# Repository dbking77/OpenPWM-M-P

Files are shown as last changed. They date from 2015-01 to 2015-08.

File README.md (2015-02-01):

OpenPWM-M-P
===========

A single channel motor driver for dc brushed motors utiliizing a attiny and a ZXBM5210 motor driver

At this time, this project is distributed under the TAPR Open Hardware License: http://www.tapr.org/ohl.html

These drivers use a resistor to control the max trip current. 

We assume that the desired trip current is right at the max for the driver, ow, 2 amps. 

Using the examples supplied in the data sheet, we would need a 0.25 ohm Rs resistor. Though, that resistor would need to be a 1 watt resistor. 

We would like to make the resistor smaller than a 1 watt surface mount resistor. So, we made the pad a 0805 pad. The max dissipation you can get out of a 0805 resistor is 1/3 watt. 

By altering VRef, we can alter the power disapated by the resistor. 

The resistor will see connect upto VRfef and ground.

If we select a lower cost resistor of 0.047 ohms ( http://www.digikey.com/scripts/DkSearch/dksus.dll?Detail&itemSeq=165686396 )

The equation for what the trip current(assuming that the trip current is 2) is:

ItripMax(2) = Vref / (Rs * 10)
2 = Vref / 0.47
Vref = 0.94V

The resistor should only see 0.04 watts if Vref is kept to 0.94.

Project owned by Michael Gregg(mgregg@-at-@michaelgregg.com) and Derr(dbking77@-at@gmail.com)

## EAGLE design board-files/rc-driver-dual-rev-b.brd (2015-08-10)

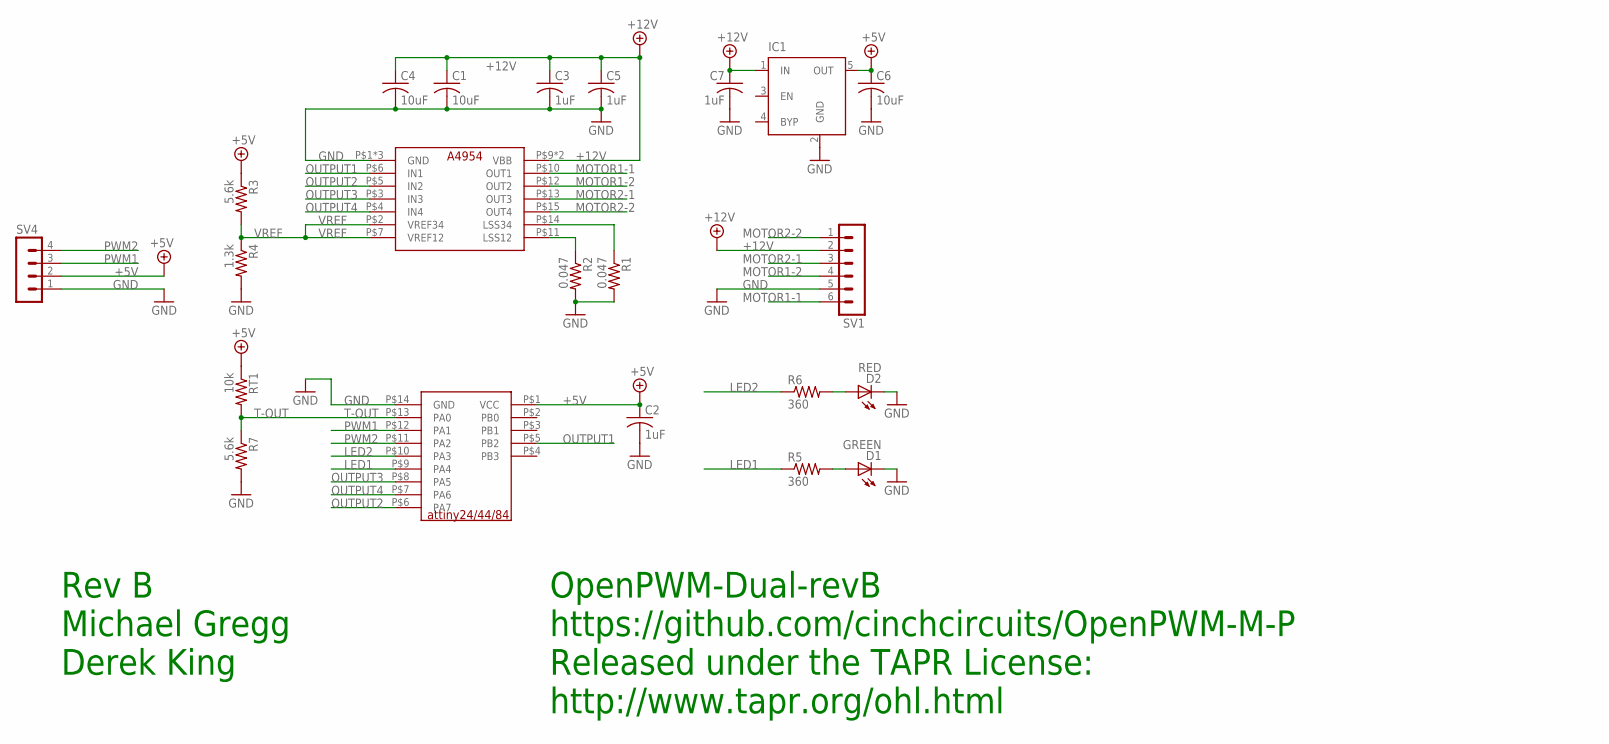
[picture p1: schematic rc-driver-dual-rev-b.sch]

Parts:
C1, C4, C6: 10uF; C1206
C2, C3, C5, C7: 1uF; C0603
D1: GREEN; CHIPLED_0603
D2: RED; CHIPLED_0603
IC1: MIC5219XX; SOT23-5; MPN TPS70950
R1, R2: 0.047; R0805
R3, R7: 5.6k; R0603
R4: 1.3k; R0603
R5, R6: 360; R0603
RT1: 10k; R0603
SV1: MA06-1
SV4: MA04-1
U$1: ATTINY24A; SOIC-14-WIDE
U$2: A4954-DUAL-HBRIDGE; TSSOP-16-LP

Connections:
+5V: C2.1, C6.1, IC1.5 (OUT), R3.1, RT1.1, SV4.2, U$1.P$1 (VCC)
+12V: C1.1, C3.1, C4.1, C5.1, C7.1, IC1.1 (IN), SV1.2, U$2.P$9 (VBB), U$2.P$16 (VBB)
GND: C1.2, C2.2, C3.2, C4.2, C5.2, C6.2, C7.2, D1.C, D2.C, IC1.2 (GND), R1.2, R2.2, R4.2, R7.2, SV1.5, SV4.1, U$1.P$14 (GND), U$2.P$1 (GND), U$2.P$8 (GND), U$2.P$17 (GND)
LED1: R5.1, U$1.P$9 (PA4)
LED2: R6.1, U$1.P$10 (PA3)
MOTOR1-1: SV1.6, U$2.P$10 (OUT1)
MOTOR1-2: SV1.4, U$2.P$12 (OUT2)
MOTOR2-1: SV1.3, U$2.P$13 (OUT3)
MOTOR2-2: SV1.1, U$2.P$15 (OUT4)
unnamed: R1.1, U$2.P$14 (LSS34)
unnamed: R2.1, U$2.P$11 (LSS12)
unnamed: D2.A, R6.2
unnamed: D1.A, R5.2
OUTPUT1: U$1.P$5 (PB2), U$2.P$6 (IN1)
OUTPUT2: U$1.P$6 (PA7), U$2.P$5 (IN2)
OUTPUT3: U$1.P$8 (PA5), U$2.P$3 (IN3)
OUTPUT4: U$1.P$7 (PA6), U$2.P$4 (IN4)
PWM1: SV4.3, U$1.P$12 (PA1)
PWM2: SV4.4, U$1.P$11 (PA2)
T-OUT: R7.1, RT1.2, U$1.P$13 (PA0)
VREF: R3.2, R4.1, U$2.P$2 (VREF34), U$2.P$7 (VREF12)

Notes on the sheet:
OpenPWM-Dual-revB
https://github.com/cinchcircuits/OpenPWM-M-P
Released under the TAPR License:
http://www.tapr.org/ohl.html
Rev B
Michael Gregg
Derek King

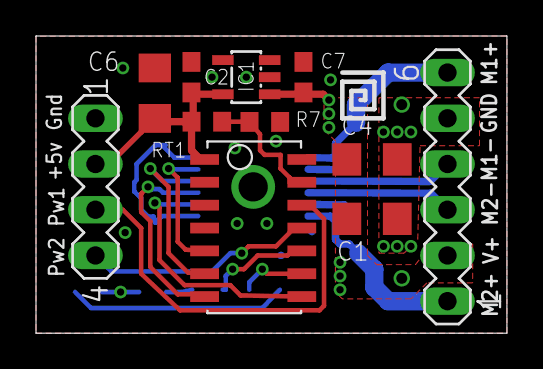
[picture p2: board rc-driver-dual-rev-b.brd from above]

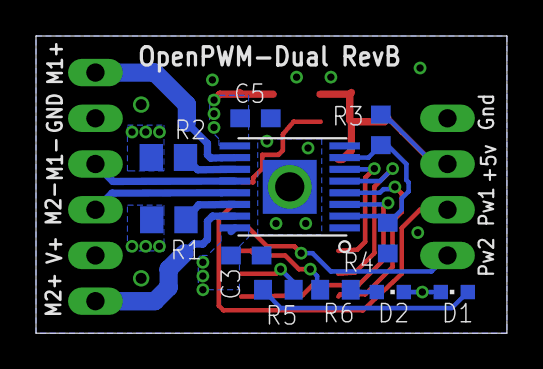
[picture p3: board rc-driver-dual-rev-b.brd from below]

Board: 2 copper layers, 26.2 x 16.5 mm, 22 parts (11 on the bottom side), 21 nets.

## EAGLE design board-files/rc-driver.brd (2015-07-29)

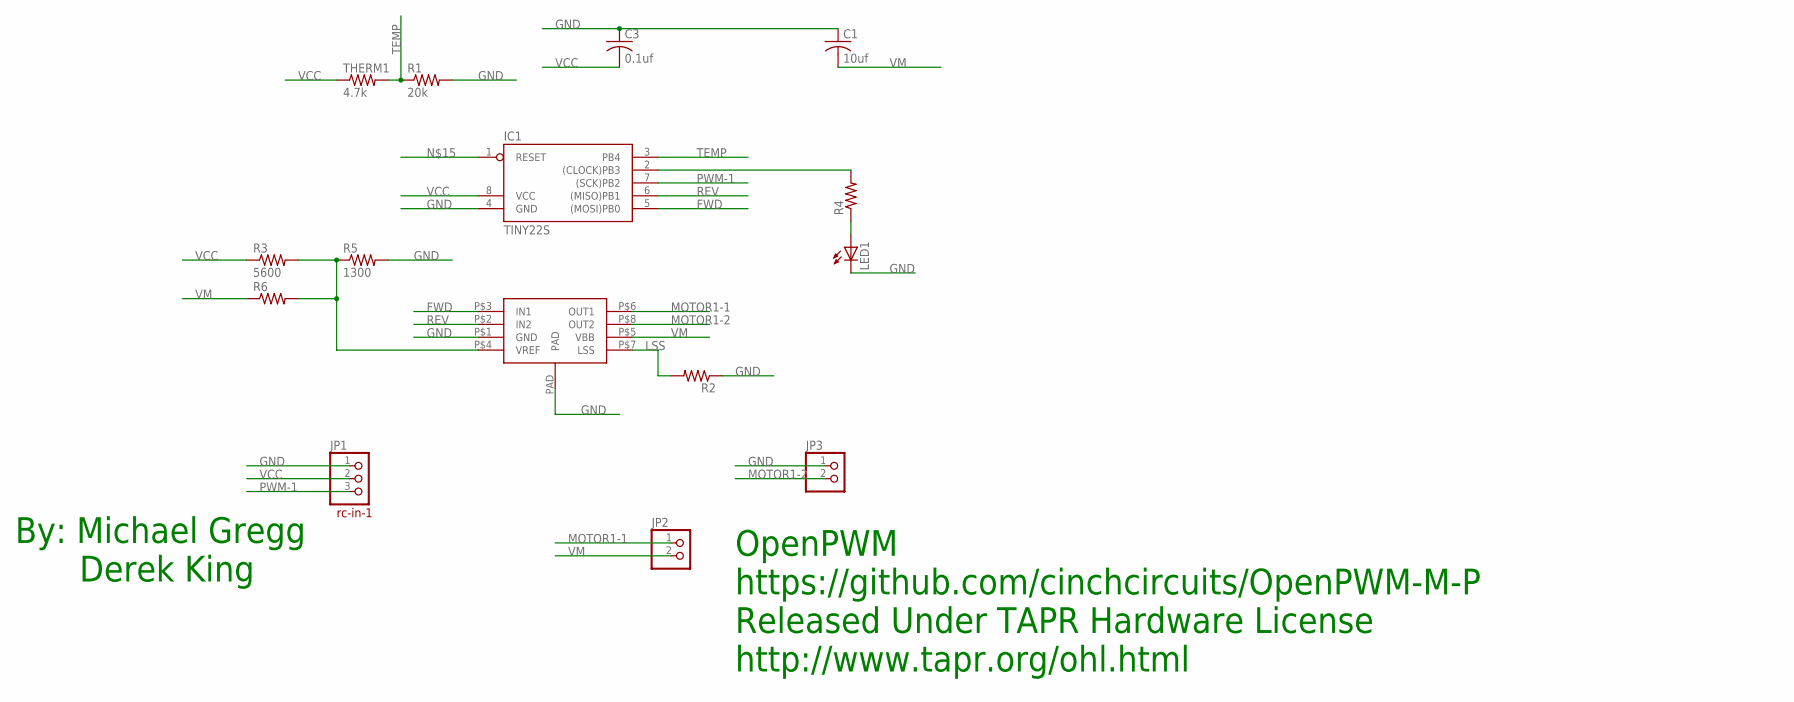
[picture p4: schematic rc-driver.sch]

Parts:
C1: 10uf; C1210
C3: 0.1uf; C0805
IC1: TINY22S; SOIC8
JP1: PINHD-1X3; 1X03
JP2, JP3: PINHD-1X2; 1X02
LED1: LEDCHIP-LED0603; CHIP-LED0603
R1: 20k; R0603
R2: R-US_R0805W; R0805W
R3: 5600; R0603
R4, R6: R-US_R0603; R0603
R5: 1300; R0603
THERM1: 4.7k; R0603
U$1: A4950-HBRIDGE; SO-8EP

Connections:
FWD: IC1.5 ((MOSI)PB0), U$1.P$3 (IN1)
GND: C1.1, C3.1, IC1.4 (GND), JP1.1, JP3.1, LED1.C, R1.2, R2.1, R5.2, U$1.P$1 (GND), U$1.PAD
LSS: R2.2, U$1.P$7 (LSS)
MOTOR1-1: JP2.1, U$1.P$6 (OUT1)
MOTOR1-2: JP3.2, U$1.P$8 (OUT2)
unnamed: R3.2, R5.1, R6.2, U$1.P$4 (VREF)
unnamed: IC1.2 ((CLOCK)PB3), R4.2
unnamed: LED1.A, R4.1
PWM-1: IC1.7 ((SCK)PB2), JP1.3
REV: IC1.6 ((MISO)PB1), U$1.P$2 (IN2)
TEMP: IC1.3 (PB4), R1.1, THERM1.2
VCC: C3.2, IC1.8 (VCC), JP1.2, R3.1, THERM1.1
VM: C1.2, JP2.2, R6.1, U$1.P$5 (VBB)

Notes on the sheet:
rc-in-1
By: Michael Gregg
Derek King
OpenPWM
https://github.com/cinchcircuits/OpenPWM-M-P
Released Under TAPR Hardware License
http://www.tapr.org/ohl.html

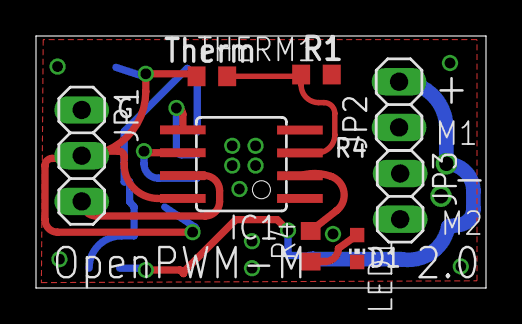
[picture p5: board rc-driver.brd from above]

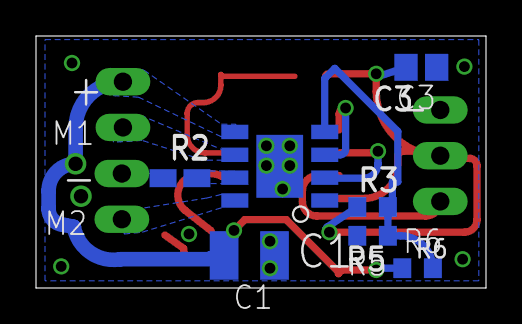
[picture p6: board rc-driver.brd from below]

Board: 2 copper layers, 25.0 x 14.0 mm, 15 parts (7 on the bottom side), 13 nets.

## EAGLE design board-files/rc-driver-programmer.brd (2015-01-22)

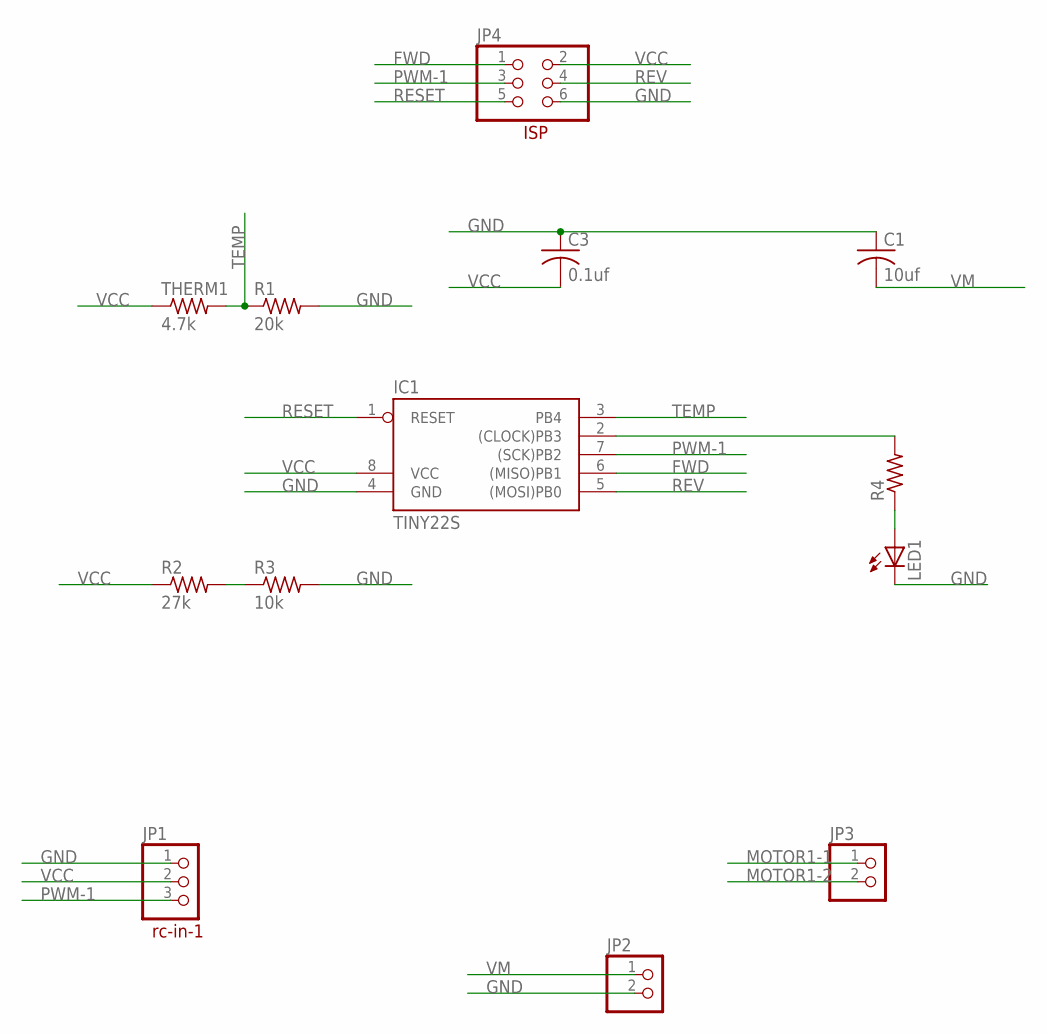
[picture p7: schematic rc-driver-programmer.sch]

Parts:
C1: 10uf; C1210
C3: 0.1uf; C0805
IC1: TINY22S; SOIC8
JP1: PINHD-1X3; 1X03
JP2, JP3: PINHD-1X2; 1X02
JP4: PINHD-2X3; 2X03
LED1: LEDCHIP-LED0603; CHIP-LED0603
R1: 20k; R0603
R2: 27k; R0603
R3: 10k; R0603
R4: R-US_R0603; R0603
THERM1: 4.7k; R0603

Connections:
FWD: IC1.6 ((MISO)PB1), JP4.1
GND: C1.1, C3.1, IC1.4 (GND), JP1.1, JP2.2, JP4.6, LED1.C, R1.2, R3.2
MOTOR1-1: JP3.1
MOTOR1-2: JP3.2
unnamed: IC1.2 ((CLOCK)PB3), R4.2
unnamed: LED1.A, R4.1
unnamed: R2.2, R3.1
PWM-1: IC1.7 ((SCK)PB2), JP1.3, JP4.3
RESET: IC1.1 (RESET), JP4.5
REV: IC1.5 ((MOSI)PB0), JP4.4
TEMP: IC1.3 (PB4), R1.1, THERM1.2
VCC: C3.2, IC1.8 (VCC), JP1.2, JP4.2, R2.1, THERM1.1
VM: C1.2, JP2.1

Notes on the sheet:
rc-in-1
ISP

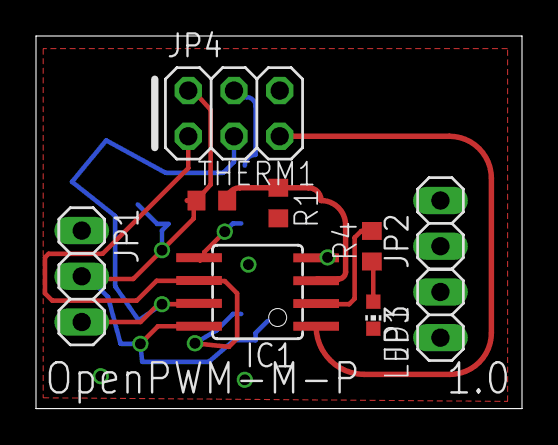
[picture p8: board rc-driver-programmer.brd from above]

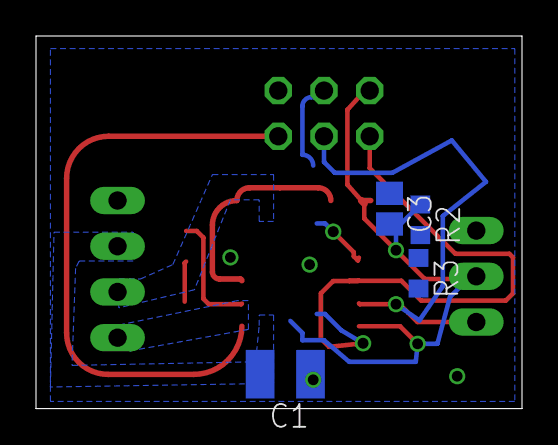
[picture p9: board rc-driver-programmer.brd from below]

Board: 2 copper layers, 27.0 x 20.7 mm, 13 parts (4 on the bottom side), 11 nets.

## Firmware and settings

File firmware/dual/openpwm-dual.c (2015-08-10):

/*
 * Copyright (c) 2015, Derek King
 * All rights reserved.
 *
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
 * THIS SOFTWARE IS PROVIDED BY THE COPYRIGHT HOLDERS AND CONTRIBUTORS "AS IS"
 * AND ANY EXPRESS OR IMPLIED WARRANTIES, INCLUDING, BUT NOT LIMITED TO, THE IMPLIED
 * WARRANTIES OF MERCHANTABILITY AND FITNESS FOR A PARTICULAR PURPOSE ARE DISCLAIMED.
 * IN NO EVENT SHALL THE COPYRIGHT HOLDER OR CONTRIBUTORS BE LIABLE FOR ANY DIRECT,
 * INDIRECT, INCIDENTAL, SPECIAL, EXEMPLARY, OR CONSEQUENTIAL DAMAGES (INCLUDING, BUT
 * NOT LIMITED TO, PROCUREMENT OF SUBSTITUTE GOODS OR SERVICES; LOSS OF USE, DATA,
 * OR PROFITS; OR BUSINESS INTERRUPTION) HOWEVER CAUSED AND ON ANY THEORY OF LIABILITY,
 * WHETHER IN CONTRACT, STRICT LIABILITY, OR TORT (INCLUDING NEGLIGENCE OR OTHERWISE)
 * ARISING IN ANY WAY OUT OF THE USE OF THIS SOFTWARE, EVEN IF ADVISED OF THE
 * POSSIBILITY OF SUCH DAMAGE.
 */

#include <stdint.h>

#define F_CPU 8000000UL
#include <util/delay.h>
#include <avr/interrupt.h>
#include <avr/io.h>

/* 
 * Getting compiler and tools (in Ubuntu)
 *  sudo apt-get update
 *  sudo apt-get install binutils-avr gcc-avr avrdude avr-libc
 */


/*
 * Fuses : want to run at 8Mhz off of internal oscillator
 * 
 * Extended Fuse Byte : 0xFF
 * unused [7:1]   
 * SELFPRGEN 0    : 1   : Self-prgromming enabled   : no
 *
 * High Fuse Byte : 11011111b = 0xDD
 * RSTDISBLE 7    : 1   : External reset disabled   : no
 * DWEN      6    : 1   : DebugWIRE active          : no
 * SPIEN     5    : 0   : Serial Program Enabled    : yes
 * WDTON     4    : 1   : Watchdog timer always on  : no
 * EESAVE    3    : 1   : EEPROM preserver on erase : no EEPROM not presevered
 * BODLEVEL [2:1] : 111 : Brownout Dectector level  : ?
 *
 * Low Fuse Byte : 11100010b = 0xE2
 * CKDIV8   7     : 1   : Clock Divided By 8        : don't divide by 8 (8Mhz internal osc)
 * CKOUT    6     : 1   : Clock output enabled      : no
 * SUT      [5:4] : 10  : Start-up time             : 14Clock cycles + 64ms
 * CLKSEL   [3:0] : 0010: Clock select              : calibrated internal osc
 *
 * http://www.engbedded.com/fusecalc/
 *  -U lfuse:w:0xe2:m -U hfuse:w:0xdf:m -U efuse:w:0xff:m
 */


/* 
 * Notes
 *   avr-gcc -print-file-name=include 
 *   g/usr/lib/gcc/avr/4.5.3/include
 *   /usr/lib/avr/include/avr/iotn24a.h
 */


// TODO have template class for this?
#define OUT1_PORT PORTB
#define OUT1_DDR DDRB
#define OUT1_PIN 2

#define OUT2_PORT PORTA
#define OUT2_DDR DDRA
#define OUT2_PIN 7

#define OUT3_PORT PORTA
#define OUT3_DDR DDRA
#define OUT3_PIN 5

#define OUT4_PORT PORTA
#define OUT4_DDR DDRA
#define OUT4_PIN 6

#define TOUT_PORT PORTA
#define TOUT_DDR DDRA
#define TOUT_PIN 0

#define PWM1_PORT PORTA
#define PWM1_DDR DDRA
#define PWM1_PIN 1

#define PWM2_PORT PORTA
#define PWM2_DDR DDRA
#define PWM2_PIN 2

// Used to indicate error has occurred
#define LED2_PORT PORTA
#define LED2_DDR DDRA
#define LED2_PIN 3

// Used to indicate that input signal is being recv'ed
#define LED1_PORT PORTA
#define LED1_DDR DDRA
#define LED1_PIN 4


void gpioInit()
{
  DDRA = 
    (0<<TOUT_PIN) |
    (0<<PWM1_PIN) |
    (0<<PWM2_PIN) |
    (1<<LED2_PIN) | 
    (1<<LED1_PIN) |
    (1<<OUT3_PIN) |
    (1<<OUT4_PIN) |
    (1<<OUT2_PIN) ;
  
  PORTA =
    (1<<PWM1_PIN) |
    (1<<PWM2_PIN) |
    (1<<LED2_PIN) |
    (1<<LED1_PIN) ;
  
  DDRB = 
    (1<<OUT1_PIN);
  
  PORTB = 0;
}

/*
 * Mapping of Timers to Outputs
 *  output1 and output2 are a pair
 *  output2 and output4 are a pair
 *  
 *  output1 : PB2 : OC0A
 *  output2 : PA7 : OC0B
 *  output3 : PA5 : OC1B
 *  output4 : PA6 : OC1A
 */


/**
 * Set duty for motor1 (out1 and out2)
 *    value of 255 = full forward
 *    value of -255 = full reverse
 *    value of 0 = stop/brake
 * 
 * out1 = PB2 = OC0A
 * out2 = PA7 = OC0B
 */
void setMotor1(int16_t duty)
{
  // Enable outputs, by enable PWM control of pins
  // set A & B outputs to non-inverting (for fast PWM)
  // in non-inverting mode pins are SET at BOTTOM
  enum { T0_COMv = 2 }; 
  TCCR0A |= (T0_COMv<<COM0A0) | (T0_COMv<<COM0B0);

  // Staturate duty between -0xFF and 0xFF
  if (duty > 0xFF)
  {
    duty = 0xFF;
  }
  else if (duty < -0xFF)
  {
    duty = -0xFF;
  }

  if (duty < 0)
  {
    OCR0A = duty-1;
    OCR0B = 0xFF; // 0xFF high always
  }
  else 
  {    
    OCR0A = 0xFF; // 0xFF high always
    OCR0B = -duty-1;
  }
}

/**
 * Set duty for motor2 (out3 and out4)
 *    value of 255 = full forward
 *    value of -255 = full reverse
 *    value of 0 = stop/brake
 * 
 * out3 = PA5 = OC1B
 * out4 = PA6 = OC1A
 */
void setMotor2(int16_t duty)
{
  // Enable outputs, by enable PWM control of pins
  // set A & B outputs to non-inverting (for fast PWM)
  // in non-inverting mode pins are set at BOTTOM, and cleared on compare match
  enum { T1_COMv = 2 }; 
  TCCR1A |= (T1_COMv<<COM1A0) | (T1_COMv<<COM1B0);

  // Staturate duty between -0xFF and 0xFF
  if (duty > 0xFF)
  {
    duty = 0xFF;
  }
  else if (duty < -0xFF)
  {
    duty = -0xFF;
  }

  if (duty < 0)
  {
    OCR1A = 0xFF&(duty-1);
    OCR1B = 0xFF; // 0xFF high always
  }
  else 
  {    
    OCR1A = 0xFF; // 0xFF high always
    OCR1B = 0xFF&(-duty-1);
  }
}


void disableMotors()
{
  // Disable outputs be switching pins to normal operation.
  // Out1 and out2 will PORT are already set to 0, so output will
  // high-Z and motor will coast
  TCCR0A &= 0x0F;  // Clears COM0A and COM0B (top 4 bits)
  TCCR1A &= 0x0F;
}



volatile uint8_t tim0_ovf_count = 0;
volatile char tim0_ovf_flag;
ISR(TIM0_OVF_vect)
{
  tim0_ovf_flag = 1;
  ++tim0_ovf_count;
}



// Prevent compiler from moving memory access operations across this code
#define MEMBAR() __asm volatile( "" ::: "memory" );

/** This struct allows use to create 16bit value from two 8bit values.
 *  It assumes that avrgcc organizes memory in little-endian order
 *
 * AVR uses 8bit registers, so 16bit value is stored two 8bit register
 * The typical code to concatinate two 8bit values into 16bit values is:
 *  
 *  uint8_t lo,hi;
 *  uint16_t result = (hi<<8) | lo;
 * 
 * The above code really shouldn't produce any assembly, because its just
 * shuffling around registers but it does:
 *    166:	83 2f       	mov	r24, r19
 *    168:	90 e0       	ldi	r25, 0x00	; 0
 *    16a:	92 2b       	or	r25, r18
 *    16c:	90 93 6d 00 	sts	0x006D, r25
 *    170:	80 93 6c 00 	sts	0x006C, r24
 *
 * If the union is used instead, the assembly looks like
 *    176:	c3 2f       	mov	r28, r19
 *    178:	d2 2f       	mov	r29, r18
 *    17a:	d0 93 6d 00 	sts	0x006D, r29
 *    17e:	c0 93 6c 00 	sts	0x006C, r2
 */
union Timer16
{
  uint16_t val;
  struct 
  {
    uint8_t lo,hi;
  };
};



/**
 * Returns 16bit timestamp generated from TCNT0
 */
uint16_t getTimestamp()
{
  union Timer16 cnt;
  cnt.lo = TCNT0;
  MEMBAR();
  cnt.hi = tim0_ovf_count;
  MEMBAR();
  uint8_t tifr = TIFR0;
  MEMBAR();

  // A servo PWM pulse is typically between 1.0 and 2.0 ms long.
  // Since clock is 8Mhz, this a 2.0ms pulse is 16000 cycles.
  // Unfortunately TIM0 is only 8bit (and TIM1 is set to only count to 8bit).
  // Just using the TCNT0 value to measure pulse width is not enough.
  // 
  // To generate top 8bits of 16bit time value, the timer overflow interrupt to
  // increment an 8bit overflow counter.  
  // Typically concatinating the overflow counter 8bit TCNT0 value produces 
  // will prodcue the correct overflow count.  
  // However, the is a race condition where the TNCT timer has overflowed
  // but the ISR has not run to increment the counter.
  // In this case the timer overflow flag will be set and TCNT will have a low
  // value.  In this case, the code should add 1 to the counter before using it.
  // There is is also the possibility that the timer overflows just after TCNT
  // is read, in this case the overflow flag will be set, and TCNT will be high,
  // in this case the overflow counter is correct.
  if ((tifr & (1<<TOV0)) && (cnt.lo & 0x80))
  {
    ++cnt.hi;
    // debug toggle LED everytime this occurs
    //LED2_PORT ^= (1<<LED2_PIN);
  }
  return cnt.val;
}


struct ServoPwm
{
  // pulse width measurement value of 8000 = 1ms.
  // value of zero is special and indicates valid value
  volatile uint16_t pulse_width;
  int16_t average_pulse_width;
  uint16_t rising_edge_time;
  volatile uint8_t no_signal_cycles;
  char valid_rising_edge; // true if rising edge was captured recently
} pwm1, pwm2;

// Clock frequency is 8Mhz, centered pulse width is usually 1.5ms
//   1.5ms = 1500us :  1500us * 8Mhz = 1500*8
//   DX5e output varies from 1.1 to 1.9ms
enum 
{
  MIN_VALID_SERVO_PULSE_WIDTH = 800*8, 
  CENTER_SERVO_PULSE_WIDTH    = 1500*8,
  MAX_VALID_SERVO_PULSE_WIDTH = 2200*8,
  SERVO_DEADZONE_WIDTH        = 100*8,
};

// Number of 2ms cycles before servo signal is assumed to be *lost*
enum {LOST_SERVO_SIGNAL_CYCLES=100};

/**
 * Should be called from mainloop about every 2milliseconds, in order to 
 * detect bad pulse-widths or a loss of servo signal
 * 
 * returns true if servo signal seems to be lost
 */
char timeoutServoPwm(struct ServoPwm* pwm, uint16_t time)
{
  // Since clock runs at 8Mhz, every 8.192ms the 16bit timestamp will wrap around.
  // Any pulse longer than 8.192ms will not be measured properly because
  // the difference between rising and falling edges will be large than a 16bit value
  //
  // Instead a long pulse width will alias as a shorter measurement.
  // For example a 9.192ms pulse will be alias to a 1ms pulse.
  // This means invalid pulse widths might seems to be valid.  
  // To prevent longer pulse from aliasing to shorter values, this code will
  // measure the difference between the current time, and last rising edge time,
  // if the time difference is larger than the MAX_VALID_SERVO_PULSE_WIDTH, 
  // it will clear the valid_rising_edge flag
  if (pwm->valid_rising_edge) 
  {
    uint16_t width = time - pwm->rising_edge_time;
    if (width > MAX_VALID_SERVO_PULSE_WIDTH)
    {
      pwm->valid_rising_edge = 0;
    }
  }

  // every time this is called to increment no signal cycles
  cli();
  uint8_t no_signal_cycles = pwm->no_signal_cycles+1;
  char lost_signal = (no_signal_cycles >= LOST_SERVO_SIGNAL_CYCLES);
  if (!lost_signal)
  {
    // only write value back if it has not overran
    pwm->no_signal_cycles = no_signal_cycles;
  }
  sei();
      
  return lost_signal;
}


/** 
 * Called from pin-change interrupt for rising or falling edge of servo pwm
 */
void updateServoPwm(struct ServoPwm* pwm, uint16_t time, char rising)
{
  if (rising)
  {
    // rising edge
    pwm->valid_rising_edge = 1;
    pwm->rising_edge_time = time;    
  }
  else if (pwm->valid_rising_edge)
  {
    pwm->valid_rising_edge = 0;
    // falling edge with valid rising edge, determine pulse width
    uint16_t width = time - pwm->rising_edge_time;
    if ((width >= MIN_VALID_SERVO_PULSE_WIDTH) && (width <= MAX_VALID_SERVO_PULSE_WIDTH))
    {
      // pulse width seems valid
      pwm->pulse_width = width;
      pwm->no_signal_cycles = 0;
    }
    else
    {
      // debug toggle LED when bad pulse width is seen
      // LED1_PORT ^= (1<<LED1_PIN);
    }
  }
}

/** Get servo pulse width 
 * pulse width is rescaled and has a dead-zone removed
 */
int16_t getAvgServoPulseWidth(struct ServoPwm *pwm)
{
  // make sure read of pulse width is atomic
  cli();
  int16_t new_width = pwm->pulse_width;
  sei();

  int16_t width = pwm->average_pulse_width;
  width += (new_width-width)>>4;
  pwm->average_pulse_width = width;

  // offset pulse widths so values so output   
  width-=CENTER_SERVO_PULSE_WIDTH;
  
  if (width > SERVO_DEADZONE_WIDTH)
  {
    width -= SERVO_DEADZONE_WIDTH;
  }
  else if (width < -SERVO_DEADZONE_WIDTH)
  {
    width += SERVO_DEADZONE_WIDTH;
  }
  else
  {
    width = 0;
  }
  return width;
}



/**
 * Use pin change interrupt and TIM0 to measure input PWM pulse width
 * this uses a combination of TCNT0 and TIM0 overflow interrupt to
 * generate a 16bit timestamp value that alows a servo pulse between
 * 1 and 2ms to be measured.
 * 
 * PA1 : PWM1 : PCINT1
 * PA2 : PWM2 : PCINT2
 */
uint8_t pcint_last_in;
ISR(PCINT0_vect)
{
  // Read hardware registers immediately and in exact order specified
  uint8_t in = PINA; // read pin A
  MEMBAR();
  uint16_t time = getTimestamp();

  // The pin change interrupt could be triggered by
  // and change of one or both PWM pins, use difference between
  // last and current pin values to determine which pins changed
  uint8_t changed = in ^ pcint_last_in;
  pcint_last_in = in;  

  if (changed & (1<<PWM1_PIN))
  {
    char rising_edge = (in & (1<<PWM1_PIN));
    updateServoPwm(&pwm1, time, rising_edge);
  }

  if (changed & (1<<PWM2_PIN))
  {
    char rising_edge = (in & (1<<PWM2_PIN));
    updateServoPwm(&pwm2, time, rising_edge);
  }
}


int main(void)
{
  gpioInit();

  // Enable PWM mode on timer 0 without actually enabling outputs
  enum { T0_WGMv = 3 }; //fast PWM mode use 0xFF as TOP
  enum { T0_CSv = 1 };  //use internal clock with no prescalling
  // Enable Timer/Counter0 outputs 
  TCCR0A = (T0_WGMv&3);
  TCCR0B = ((T0_WGMv>>2)<<WGM02) | T0_CSv;

  // Enable PWM mode on timer 1.  Have timer saturate at 0xFF
  enum { T1_WGMv = 5 }; //fast PWM mode use 0xFF as TOP
  enum { T1_CSv = 1 };  //use internal clock with no prescalling
  TCCR1A = (T1_WGMv&3);
  TCCR1B = ((T1_WGMv>>2)<<WGM12) | T1_CSv;

  // Have timers run 180degrees out-of-phase to reduce supply ripple
  TCNT0 = 0;
  TCNT1 = 0x84;

  // Timer interrupt mask for timer0
  // Use timer0 overflow interrupt along with timer 0 value to
  // measure servo pwm pulse
  TIMSK0 = (1<<TOIE0);  

  // Enabled PCINT1 and PCINT2 for PA1 and PA2 pin change interrupts
  PCMSK0 = (1<<PCINT1) | (1<<PCINT2);
  GIMSK = (1<<PCIE0);
  pcint_last_in = PINA;

  // Enable interrupts
  sei();

  uint8_t stable_counter = 0;
  uint8_t ovf_counter = 0;
  while (1)
  {
    if (tim0_ovf_flag)
    {
      tim0_ovf_flag = 0;
      ++ovf_counter;      
      if (ovf_counter > 62)
      {
        ovf_counter = 0;
        //LED1_PORT ^= (1<<LED1_PIN);
        // when overflow counter reaches 62 it means about 
        // 62*256/8Mhz = 1.984ms have elapsed
        uint16_t time = getTimestamp();
        if (timeoutServoPwm(&pwm1, time) || timeoutServoPwm(&pwm2, time))
        {
          // servo signals stopped comming in, disable motors
          LED1_PORT &= ~(1<<LED1_PIN);
          LED2_PORT |= (1<<LED2_PIN);
          disableMotors();
          stable_counter = 0;
        }
        else 
        {
          LED1_PORT |= (1<<LED1_PIN);
          LED2_PORT &= ~(1<<LED2_PIN);

          // calculate new duty values from servo values
          // assume:
          //  pwm2 = forward/reverse
          //  pwm1 = rotate
          int16_t forward = getAvgServoPulseWidth(&pwm2);
          int16_t rotate  = getAvgServoPulseWidth(&pwm1);

          // range on forward and reverse values is typically 
          // -400*8 to 400*8 for Spektrum DX5 and 8Mhz clock

          // scale forward value  so that max forward value 400*8 is now 1024
          forward = (forward * 5)>>4;
          
          // scale rotate so that that max value 400 is now 1024
          rotate = (rotate * 5)>>4;

          int16_t duty1 = forward + rotate;
          int16_t duty2 = forward - rotate;

          if (stable_counter < 100)
          {
            ++stable_counter;
          }
          else
          {
            setMotor1(-duty1>>2);
            setMotor2(duty2>>2);
          }
        }
      } // end if (ovf_counter > 62)
    } // end if (tim0_ovf_flag)

  } // end while(1)

  return 0;
}

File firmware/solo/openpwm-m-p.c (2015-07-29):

/*
 * Copyright (c) 2015, Derek King
 * All rights reserved.
 *
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
 * THIS SOFTWARE IS PROVIDED BY THE COPYRIGHT HOLDERS AND CONTRIBUTORS "AS IS"
 * AND ANY EXPRESS OR IMPLIED WARRANTIES, INCLUDING, BUT NOT LIMITED TO, THE IMPLIED
 * WARRANTIES OF MERCHANTABILITY AND FITNESS FOR A PARTICULAR PURPOSE ARE DISCLAIMED.
 * IN NO EVENT SHALL THE COPYRIGHT HOLDER OR CONTRIBUTORS BE LIABLE FOR ANY DIRECT,
 * INDIRECT, INCIDENTAL, SPECIAL, EXEMPLARY, OR CONSEQUENTIAL DAMAGES (INCLUDING, BUT
 * NOT LIMITED TO, PROCUREMENT OF SUBSTITUTE GOODS OR SERVICES; LOSS OF USE, DATA,
 * OR PROFITS; OR BUSINESS INTERRUPTION) HOWEVER CAUSED AND ON ANY THEORY OF LIABILITY,
 * WHETHER IN CONTRACT, STRICT LIABILITY, OR TORT (INCLUDING NEGLIGENCE OR OTHERWISE)
 * ARISING IN ANY WAY OUT OF THE USE OF THIS SOFTWARE, EVEN IF ADVISED OF THE
 * POSSIBILITY OF SUCH DAMAGE.
 */

#include <stdint.h>

#define F_CPU 8000000UL
#include <util/delay.h>
#include <avr/interrupt.h>
#include <avr/io.h>

/* 
 * Getting compiler and tools (in Ubuntu)
 *  sudo apt-get update
 *  sudo apt-get install binutils-avr gcc-avr avrdude avr-libc
 */


/*
 * Fuses : want to run at 8Mhz off of internal oscillator
 * 
 * Extended Fuse Byte : 0xFF
 * unused [7:1]   
 * SELFPRGEN 0    : 1   : Self-prgromming enabled   : no
 *
 * High Fuse Byte : 11011111b = 0xDF
 * RSTDISBLE 7    : 1   : External reset disabled   : no
 * DWEN      6    : 1   : DebugWIRE active          : no
 * SPIEN     5    : 0   : Serial Program Enabled    : yes
 * WDTON     4    : 1   : Watchdog timer always on  : no
 * EESAVE    3    : 1   : EEPROM preserver on erase : no EEPROM not presevered
 * BODLEVEL [2:1] : 111 : Brownout Dectector level  : ?
 *
 * Low Fuse Byte : 11100010b = 0xE2
 * CKDIV8   7     : 1   : Clock Divided By 8        : don't divide by 8 (8Mhz internal osc)
 * CKOUT    6     : 1   : Clock output enabled      : no
 * SUT      [5:4] : 10  : Start-up time             : 14Clock cycles + 64ms
 * CLKSEL   [3:0] : 0010: Clock select              : calibrated internal osc
 *
 * http://www.engbedded.com/fusecalc/
 *  -U lfuse:w:0xe2:m -U hfuse:w:0xdf:m -U efuse:w:0xff:m
 */


/* 
 * Notes
 *   avr-gcc -print-file-name=include 
 *   g/usr/lib/gcc/avr/4.5.3/include
 *   /usr/lib/avr/include/avr/iotn25.h
 */


/* Pin numbering defs */
enum {
  REV_PIN=0,  // reverse output pin
  FWD_PIN=1,  // forward output pin 
  PWM_PIN=2,  // server pwm input pin
  LED_PIN=3,  
  TEMP_PIN=4  // connected to temperature thermistor
};



/**
 * Set duty of motor output
 *    value of 255 = full forward
 *    value of -255 = full reverse
 *    value of 0 = stop/brake
 */
void setMotorOutput(int16_t duty)
{
  // Enable Timer/Counter0 outputs 
  enum { T0_COMv = 2 }; //non-inverting (for fast PWM)
  TCCR0A |= (T0_COMv<<COM0A0) | (T0_COMv<<COM0B0);

  if (duty>0xFF)
  {
    duty = 0xFF;
  }
  else if (duty < -0xFF)
  {
    duty = -0xFF;
  }

  if (duty < 0)
  {
    OCR0A = duty-1;
    OCR0B = 0xFF; // 0xFF high always
  }
  else 
  {    
    OCR0A = 0xFF; // 0xFF high always
    OCR0B = -duty-1;
  }
}


/**
 * Disables motor output : effectivly high-Z outputs
 *  When both REV and FWD inputs to motor are low the motor driver disables its outputs
 *  Because of how the PWM signals are generated, a always low output cannot be generated,
 *  So 
 */
void disableMotor()
{
  // disable both timer outputs by setting botCOM0A/B to 0
  TCCR0A &= 0x0F;
}

/// Updated by times
volatile uint8_t g_pwm_pulse_width = 0;

/// number of times PWM overflow between getting pulses
uint8_t g_pwm_overflow_count = 0;

/// Used by main loop for flashing LED
volatile char g_overflow_flag = 0;

ISR(TIMER1_OVF_vect)
{
  g_overflow_flag = 1;
  if (g_pwm_overflow_count < 250)
  {
    ++g_pwm_overflow_count;
  }
  else 
  {
    // if the timer has overflowed for more than 200 times 
    // then it has been 0.5seconds since the last good pwm pulse was recieved, 
    // and the motors output should be disabled
    g_pwm_pulse_width = 0;
  }
}

ISR(INT0_vect)
{
  static uint8_t pwm_rising_edge = 0;
  // Flash LED
  if (PINB & (1<<PWM_PIN))
  {    
    // rising edge of PWM
    pwm_rising_edge = TCNT1;
    g_pwm_overflow_count = 0;
  }
  else
  {
    // falling edge of PWM
    if (g_pwm_overflow_count < 2)
    {
      // if overflow count is more than 1 then this was not a valid pulse width
      g_pwm_pulse_width = TCNT1 - pwm_rising_edge;
    }    
  }
}


int main(void)
{
  // Enable PWM mode on timer 0 without actually enabling outputs
  enum { T0_WGMv = 3 }; //fast PWM mode use 0xFF as TOP
  TCCR0A = (T0_WGMv&3);
  enum { T0_CSv = 1 };  //use internal clock with no prescalling
  TCCR0B = ((T0_WGMv>>2)<<WGM02) | T0_CSv;

  // Initialize Timer/Counter1 as free-running 0 to 0xFF
  // Pin change interrupt will read timer value on rising and falling edges 
  // and compare values to get pulse width. 
  // 
  // Have timer prescaled so that its period is longer than the longest
  // valid servo WPM pulse width that needs to be measured (2ms).
  //   2ms * 8Mhz / 256 = 62.5 --> set clock divider to 64
  enum { T1_CSv = 7 };  //use devide clock by 64
  TCCR1 = T1_CSv;  // all other bits are 0
  GTCCR = 0;
  PLLCSR = 0; // don't use external clock for timer1

  // Timer interrupt mask (for timer0 and timer1)
  // Use timer1 overflow interrupt to detect loss of servo PWM input signal
  TIMSK = (1<<TOIE1);  
  
  // PORTB data direction
  // 0 : REV  : output
  // 1 : FWD  : output
  // 2 : PWM  : input w/ pullup
  // 3 : LED  : output
  // 4 : TEMP : input
  DDRB = (1<<REV_PIN) | (1<<FWD_PIN) | (1<<LED_PIN);
  PORTB = (1<<LED_PIN) | (1<<PWM_PIN);

  // Enable int0 interrupt, on both rising and falling edges
  MCUCR = (MCUCR & 0xFC) | 1; 
  GIMSK = (1<<INT0);

  // Enable interrupts
  sei();


  int16_t filtered_duty = 0;
  uint8_t flash_count = 0;
  while (1)
  {
    // Count 2ms overflows to determine when to flash LED
    if (g_overflow_flag)
    {
      g_overflow_flag = 0;
      ++flash_count;

      // pwm pulse width is volatile (changed by interrupt) so read it only once before using it
      int16_t pulse_width = g_pwm_pulse_width; 
      if (pulse_width == 0)
      {
        PORTB |= (1<<LED_PIN);
        disableMotor();
        filtered_duty = 0;
      }
      else 
      {
        // Scale and offset PWM pulse with so that 1.9us pulse produces duty of 255, 
        //   and 1.1ms pulse produces duty of -255
        // 1 LSB of pulse width is nominally 8uSec ( 1/8Mhz * 64 = 8usec)
        // zero throttle is about 1.5ms, which is 187.5 (1.5msec/8usec = 187.5)
        int16_t duty = (int16_t)pulse_width - 187;

        // Range on PWM pulse is 1.9-1.1 = 0.8ms = 100.
        //   rescale PWM so that pulse of -50 becomes -255 and +50 becomes 255
        //   We want to multiply duty by 5.1 (255/50 = 5.1)
        //   To get same result multiple duty by 5.1*8 and shift left by 3 to divide by 8
        //     50*41>>3 = 256
        //duty = (duty*41) >> 3;
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

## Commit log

2014-12-25 Adding first version of the board files. Including the gerbers used at seeedstudio
    [rc-driver-programmer.GBL, rc-driver-programmer.GBO, rc-driver-programmer.GBP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]
2015-01-04 Servo input capture and motor output is working. Settings for avrdude firmware and fuse programming Working servo input capture code with detection of lost signal. Hard-coded scaling from servo pulse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
2015-01-04 Rescale servo input based on ranges of mixed signals from RC controller. Put filter and change limiter on PWM signal to prevent over-current caused by moving stick too quickly.
    [openpwm-m-p.c]
2015-01-13 Added start os v 2.0 files. Need to connect vref.
    [rc-driver.brd, rc-driver.sch]
2015-01-18 Adding RC net to VREF. Creating gerbers for plain board.
    [rc-driver-programmer.brd, rc-driver-programmer.sch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]
2015-01-22 Adding start of dual motor driver and library.
    [rc-driver-dual.brd, rc-driver-dual.sch]
2015-01-23 Added motor driver to dual driver board.
    [rc-driver-dual.brd, rc-driver-dual.sch]
2015-01-26 fixing attiny silk. Shortened single rc-driver board.
    [rc-driver-dual.brd, rc-driver-dual.sch, rc-driver.brd]
2015-01-27 Added license to boards. Finished routingand silks.
    [rc-driver-dual.GBL, rc-driver-dual.GBO, rc-driver-dual.GBP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]
2015-01-28 add drunken spriral
    [rc-driver-dual.brd, rc-driver-dual.sch]
2015-01-30 Move squigly lines and extra capacitance on VM.
    [rc-driver-dual.brd, rc-driver-dual.sch]
2015-01-30 Adding some final touches to the boards. Converting fonts to Vector.
    [rc-driver-dual.GBL, rc-driver-dual.GBO, rc-driver-dual.GBP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]
2015-02-12 Moving single board files to different folder.
    [rc-driver-dual.brd, rc-driver-dual.sch, rc-driver.brd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]
2015-02-14 Untested code for PWM on second motor output.
2015-02-15 Fixed edge-case bug in duty conversion.
    [openpwm-dual.c]
2015-02-15 Update duty calculation of solo output device. Got servo pwm pulse capture working. Need to implment timeout.
2015-02-15 Fixed bug in TIM1 PWM setup. Added mixing and scaling of inputs to produce pwm. Added filter and deadzone to servo pwm.
    [openpwm-dual.c]
2015-04-03 Add brown-out detection. Have code wait for stable signal before starting motors.
    [openpwm-dual.c]
2015-08-10 Changes for battlebot competition. More part information. Changed steering and forward direction mixing. Have one led for signal, and the other for no signal.
    [rc-driver-dual.brd, rc-driver-dual.sch]
2015-08-10 Add hex file so compiler is not needed to program board.
2015-08-10 Copying dual board design to start rev B.
    [rc-driver-dual-rev-b.brd, rc-driver-dual-rev-b.sch]
2015-08-10 First pass layout of revB designed that include 5V regulator Improved part outlines in library.
    [rc-driver-dual-rev-b.brd, rc-driver-dual-rev-b.sch]
